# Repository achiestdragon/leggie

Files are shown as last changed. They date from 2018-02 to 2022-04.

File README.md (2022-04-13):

# leggie

a hexapod robot

.    still work in progress not all code completed yet 

.    project suspended , the joystick code works well so is left here for others to use 
      had issues with 3d printed parts snapping , not found a good solution to this 
      so have given up on the project , as well as some other health reasons 

# progress:-

hardware build and 3d printed parts :-

.    see README.txt for hardware and printing progress status and notes

.    dc motor version ( current work in progress )

.    3d printing parts of parts 400 hrs total so far 

.    current progress (assembling)

.    TODO:- lots  , add scad/stl parts for upper body&arms

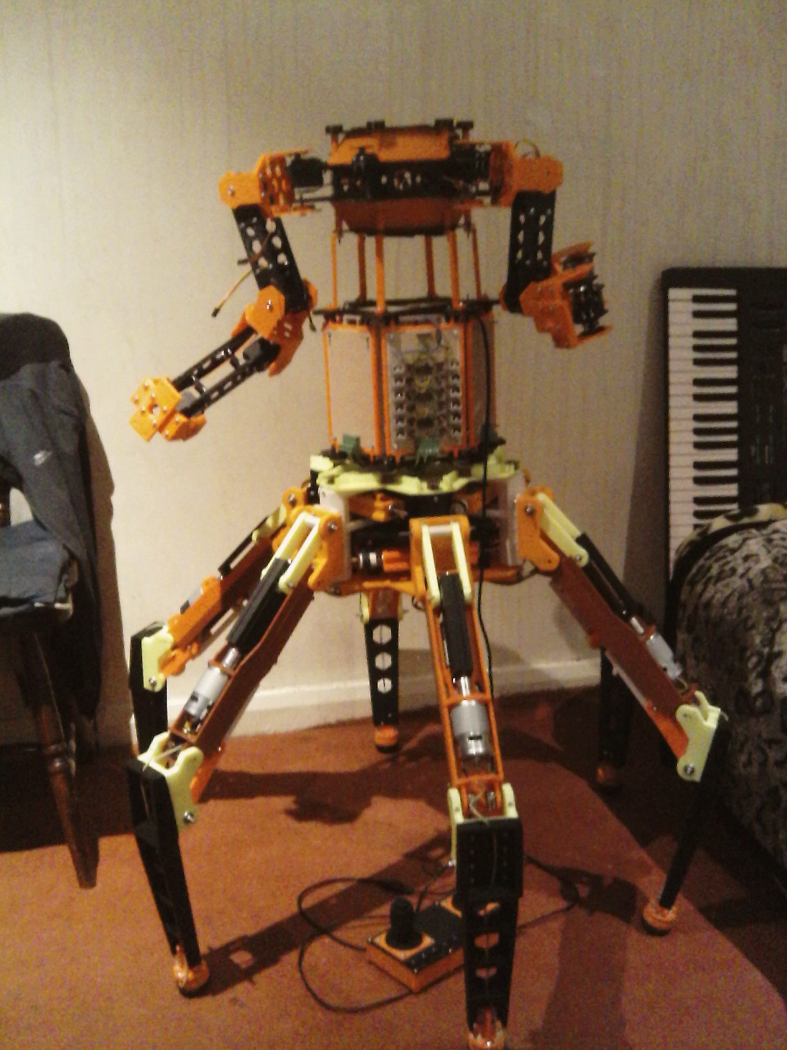
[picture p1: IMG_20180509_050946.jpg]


# code status :-

arduino nano  joystick code :-             USBjoystick1.ino       (c++)= v 1.1b  release

arduino nano  leg drive control code :-    leggie_arduino_pid.ino (c++)= v 1.0a  alpha in progress

..   rewrite pending for dc motor drive rather than pwm servo (will keep this file and add a seperate one

..   for dc motor drive pid   leggie_dc_drive.ini  (c++) = 'pending todo update'

rpi3 serial concurrent test read script :- srlpy.py (python) v 1.0a  a rough but working alpha

raspberry pi3  main control code  :-      main.py (python) v 0.9 in progress not complete

..   basic test code moves legs by joystick and a couple of preprogrammed sequences

see config_guide.txt for software setup and configuration notes

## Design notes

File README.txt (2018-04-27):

leggie  hexapod robot project version 6.0a README.txt

(c)2018 by David Powell  AKA. AchiestDragon

current version :- 6.0a  (alpha prototype)

project status
--------------

 hardware:-
    
    most of the cad redesign is done , although there's still some parts to do
  mainly , electronics covers , battery mounting , turret and head , that can
  wait for the time .
  
    there are a couple of points that may need some of the parts to be reprinted
  mainly the hip/knee joints ( with a diferent infill setting ) as a couple have
  slightly split where the pot mountings have been over tightended , although will
  see how they go as they have not totaly snapped and seem to hold well enough
    the other issues beeing the hip pivot part, this needs a hacksaw to remove on of the
  cross supports so it can actualy be assembled, in genaral all the bearing holes needed
  shaving so the bearings fitted and some of the holes in genaral also needed to be trimmed
  for it to go together.
  
    it takes about a day each to assemble a leg , including the time taken to clean up the
  3d printed parts, and about 2 days to do the main center base assembly , not including 
  print time , you need to ensure its 100 percent before fitting it as servicing it later
  is a real pain , there is an order it needs to be assembled in otherwise you will find 
  your taking it apart again ( should be covered in the assembly guide)
  
    its taken over 324 hrs of 3d printing (and about 6kg of filament used so far)
  the main base and legs of the robot are now all printed and assembled and i 
  am currently about to start work on  the dc motor drives & other electronics.
  
    once the robot can be powered up i can get back on with the software. i also 
  need to include schematics and layouts for the motor drivers and robot wireing
    
    at present im still planning to use a pi3 and adruino nanos for the robot control
  logic , but am still tempted to use a fpga for the motor timings in place of the
  arduino nanos , this is because the responce times are quicker and also the fact that the 
  fpga method can concurrently keep all the motors in sync far easyer than software
    with this in mind i need to keep the electronics more modular so it could be changed 
  if needed, the main issue here though is finding a fpga module with tool chain that
  is firstly not overly expencive and 2nd is going to be arround for some time , 
    as the same is true, of the controlers in genaral making it modular so future
  upgrades and new moddels of controlers may be used in future is also a good step
  
    this version the robot can seperate into 2 distinct parts the lower walking section
  base and legs , and the upper body section , they are joined by some spring and 3d printed 
  clips  , and connectors , that allow them to seperate , this is for transportation , 
  
    the upper electronic frame has mountings for 6 100*160 mm "eurocard" sized pcbs for the motor
  drivers (3 drivers on each ) and another for  interconnections and for the rpi3 to mount on 
  still to cad but the battery mountings , turret and head mountings will also attach to the upper
  assembly , also to cad are the covers for the electronics , but can only do these once the boards
  have been assembled so the component heights and positions can be taken into account , they may also 
  need fan mountings to keep the drivers cool 
  
    batteries , at present i have a couple of options  it needs 24 to 36v for the motors and 5v for the logic
  so i could use 2 14v and 1 7v lipo but dont realy want to have to mix types , and is the reason why i have not 
  done the cad for the battery mountings as yet 
    
    4 of the 7.4v 4000mAh or 2 of the 14.8v lipos batteries in series will give 29.6v  , an a seperate battery for
 the logic so that it does not just shutdown when the main drive power is low 
    
    the higher the voltage the faster rpm of the motors (before torque) , it could run from just 1 11.8v battery
  but it would be slow , current consumption / load is the other issue , and that relates to how long it will run 
  before you need to recharge
  
    the fact that this version is using the motors in a linear motor arrangment means all the legs hold without
  power only needing power to move , over servo versions that need power to the motors to hold there positions
  helps it run longer , the disadvantage is you cant just move the legs by hand without power to them , you have
  to turn the motor drive to get the joint to move , access to be able to do this is possible 

 software:-

    still work in progress (most of current software here relates to the servo 
  version at present and is going to be mostly rewritten )  as support for the 
  servo version is redundant long term it will be removed at some point

 history
-----------
    design history of the current hexapod robot 

    version 1  "tinybug" 
       not that tiny it used cheap satelite dish positioning jacks , suspended
    dew to being too big ( it was almost 10foot across in normal standing pose),
    power and speed with around 1kw full load, 160kg and a walk speed of about
    20 foot an hr  and 1 hr before needing to recharge the 8 x 12v 7ah lead acid gell batteries
    that took about 2 days each time, the joints where very clunky and had mountains 
    of backlash on each leg , and a mini atx controler (2010)
    
    version 2 "scare-e"
       smaller a servo version , it was fpga based and ran out of available gates in the
    fpga , so never was compleated, had 3d ultrasonics , leg movment was by pll locked state machine
    motor control sweet , ran out of gates doing the cpu , (2012)
    
    version 3 "un-named-version" 
       never got passed cad stage , sort of a hybrid concept  of a hexapd with wheels for feet
     so it could use the wheels on flat ground , or switch to walk mode and use them like feet 
     to climb up stairs , nice in concept till you try to do the stair climbing spaceings  then 
     it turns into a monster (2017)
    
    version 4 "un-named-version"
       did cad for this a dc motor version although with smaller motors but decided
      to have another go at a servo version , this one never left the drawing board
      but should of current version is a rework of the ideas i used on this (2017)

    version 5  "leggie " servo version  , scraped , servos not strong enough (2018)
    
    version 6  "leggie6" dc motor version current work in progress(2018)

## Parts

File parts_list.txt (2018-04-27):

parts list

Leggie6 parts list dc motor version
------------------------------------
this list is not complete as yet, work in progress
quant  part 
 18x   rs 775 12 to 36v dc motor 5mm shaft  
 1x    raspberry pi 3 (with 16gb microsd card for software)
 7x    arduino nano 
 36x   10k 6mm potentiometer with D shaft 
 1x    5v 3A switching regulator bec module (for pi/arduino power)
 2x    3 axis joysticks
 10x   push button switches momentary  (12mm dia hole)
 1x    10a single pole single throw on/off toggle switch
 
 3x    short usb a to mini b  cables
 1x    1.5m long usb a to mini b cable for joystick 
 
 1x    7.4v 4000mha lipo  (and suitable charger)
 2x    14.8v lipo's 4000mha (both the same type and charger )
 
 18x   15a 36v h-bridge driver modules (30a peek load) (parts list for this to be added)
 
        bearings (type 625)  5mm shaft 5mm high by 16mm outer dia
        m5 nuts and bolts  25mm thread length
        m5 threaded bar 
        
 18x   5mm to 5mm flexible shaft couplers
 
 36 x  m4 screws for the motor mountings( use screwdriver or alen key heads no room for spanner to fit)

 as needed signal wire in a number of colors
 bag of 50 cable ties (that will fit though 3mm dia holes)
 1x bag of 500 M3 bolts x 18mm long
 1x bag of 500 M3 nuts
 1x bag of 200 M3 locking nuts
 1x bag of 500 M3 washers
 6x 150mm lengths of M3 threaded bar
 10x deans connector pairs and suitable power cable
 8x strip board 100*160mm  for the electronics and motor control boards 
 some solder
 
 lots of other bits not covered yet 
 
 lots of time patience and some thought to get it working

intended for printing on a tevo delta with a 340mm dia print limit 

allow a few weeks for the printing of parts over 324 hrs 

extra parts needed for both versions
------------------------------------

for debug , testing , programming and setup you will need :-
a laptop / or pc to connect to pi3 ether ssh or vnc over wifi or bluetooth

(parts not yet defined ) 
------------------------
leds led drivers and wireing 

some sort of speaker / sounder for the onboard pi3 as it needs some way
of giving status feedback without having a display connected

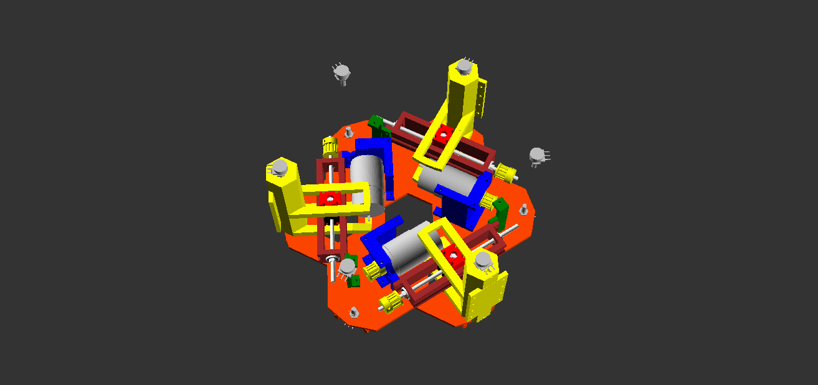
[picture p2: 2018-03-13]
scad_parts_dc_motor_version/base_asembled1.png

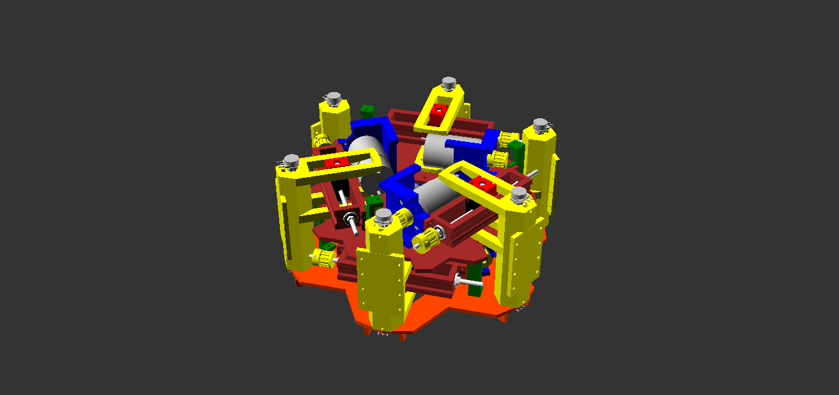
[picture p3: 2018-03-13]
scad_parts_dc_motor_version/base_asembled2.png

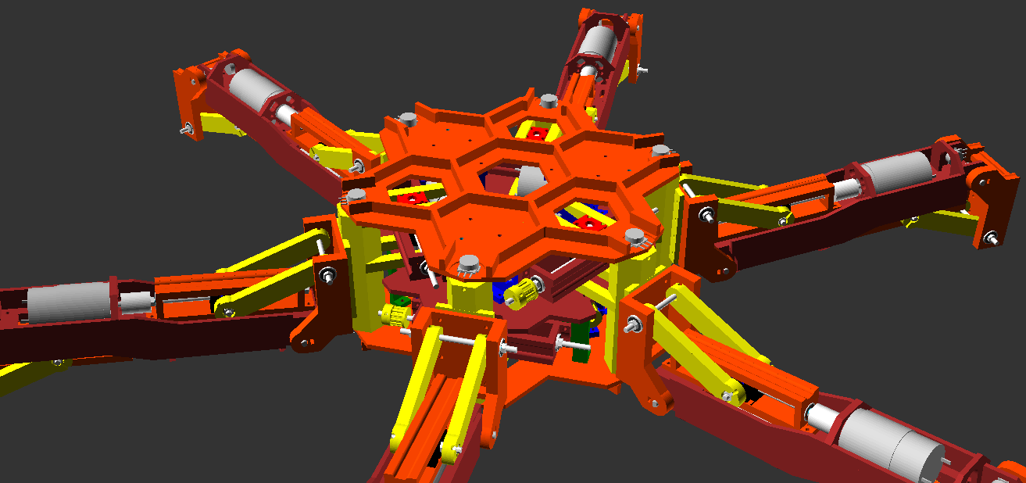
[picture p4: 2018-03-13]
scad_parts_dc_motor_version/base_asembled3.png

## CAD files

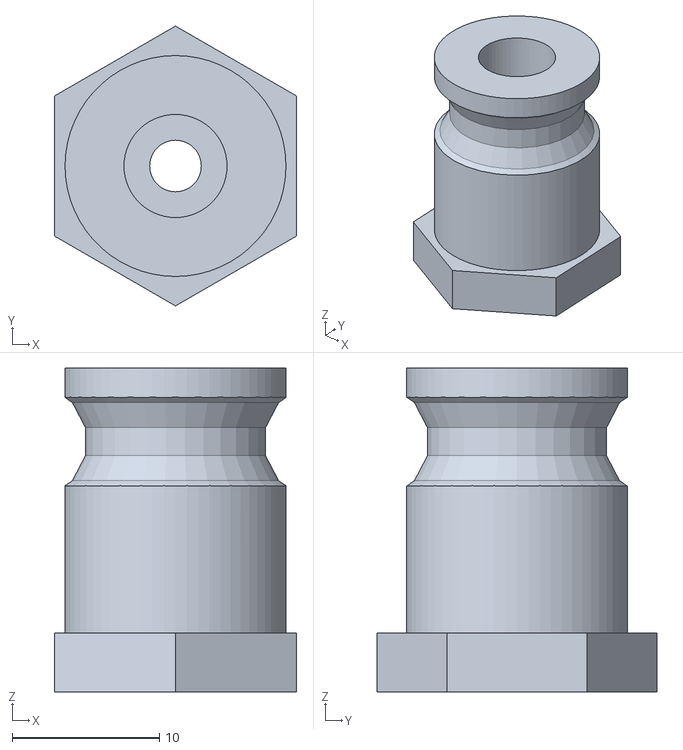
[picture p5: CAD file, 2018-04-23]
stl_parts_dc_motor_version/bodymount.stl
16.5 x 19.0 x 22.0

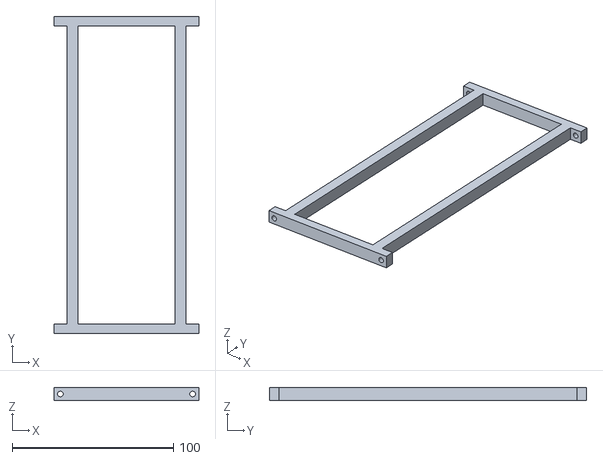
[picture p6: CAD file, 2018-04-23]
stl_parts_dc_motor_version/spacerframe.stl
90.0 x 197.0 x 8.00

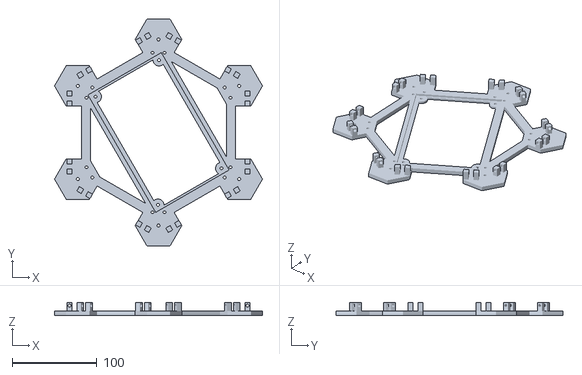
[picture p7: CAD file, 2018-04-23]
stl_parts_dc_motor_version/upperbodyt.stl
245.5 x 267.6 x 15.0

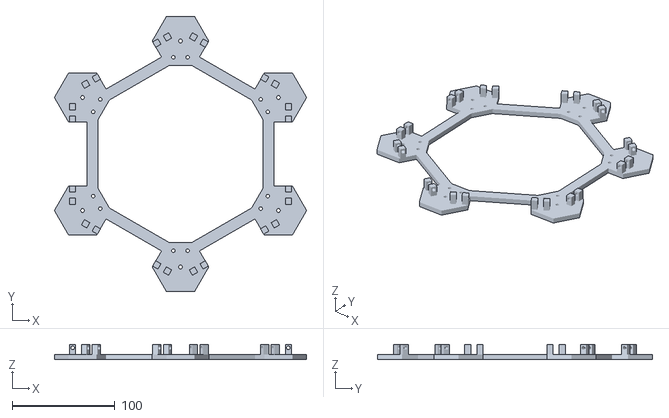
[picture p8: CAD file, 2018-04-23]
stl_parts_dc_motor_version/upperbodyb.stl
245.5 x 267.6 x 15.0

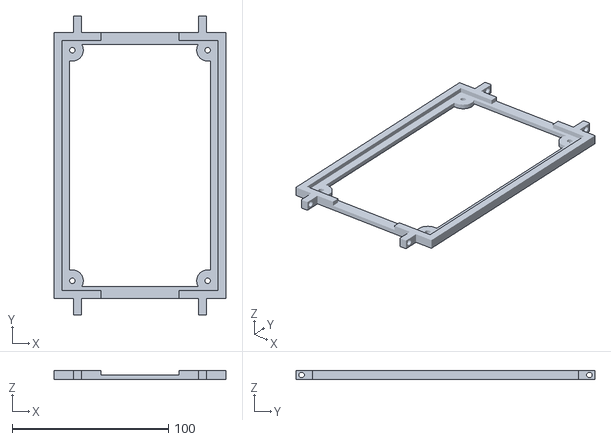
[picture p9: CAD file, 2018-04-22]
stl_parts_dc_motor_version/pcbmountframe.stl
110.0 x 191.0 x 6.00

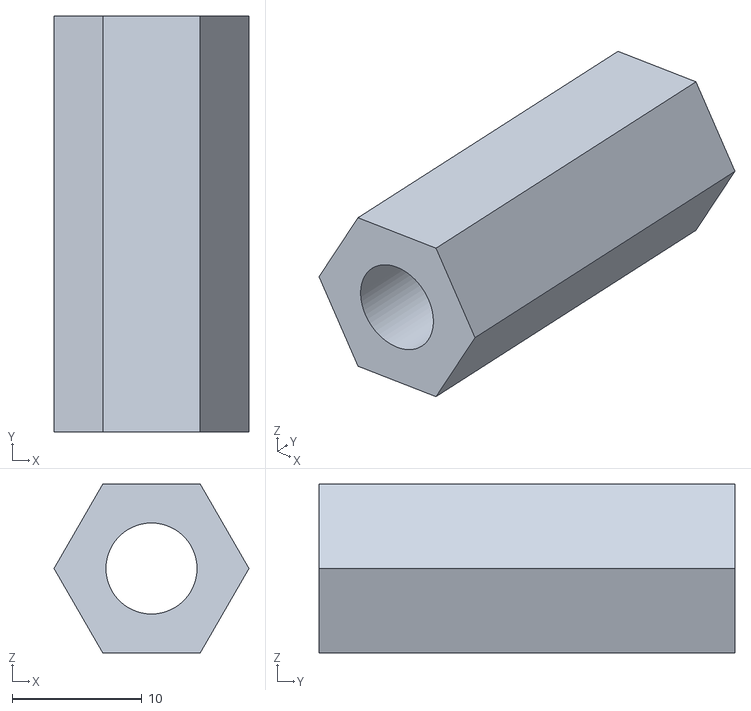
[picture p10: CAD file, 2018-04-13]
stl_parts_dc_motor_version/conrod_spacer.stl
15.0 x 32.0 x 13.0

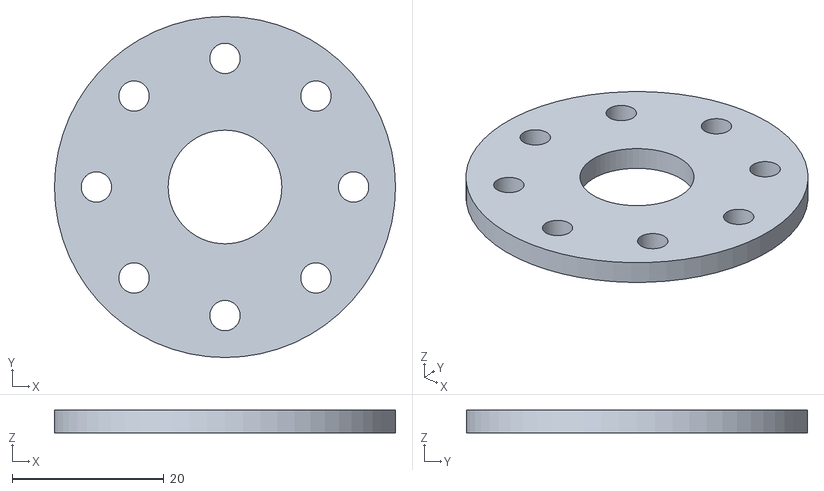
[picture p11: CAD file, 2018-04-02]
stl_parts_dc_motor_version/footsw1.stl
45.0 x 45.0 x 3.00

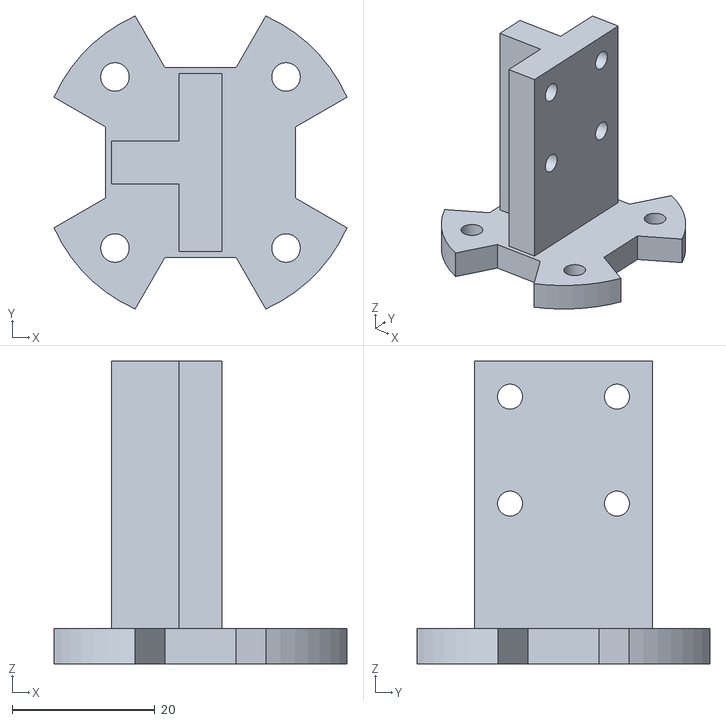
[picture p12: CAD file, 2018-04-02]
stl_parts_dc_motor_version/foot_mnt.stl
41.1 x 41.1 x 42.5

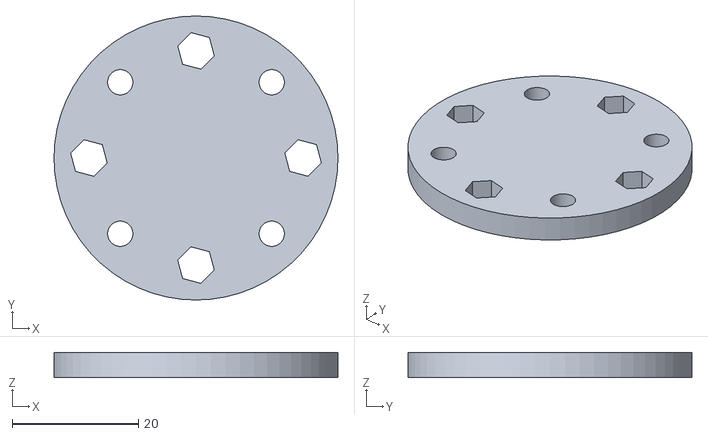
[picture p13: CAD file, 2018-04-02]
stl_parts_dc_motor_version/footsw4.stl
45.0 x 45.0 x 4.00

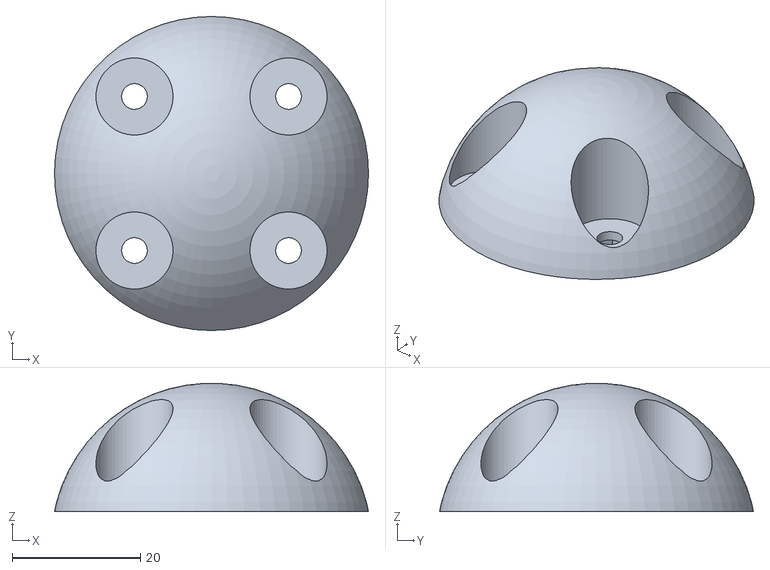
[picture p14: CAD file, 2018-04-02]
stl_parts_dc_motor_version/footpad.stl
48.9 x 48.9 x 20.0

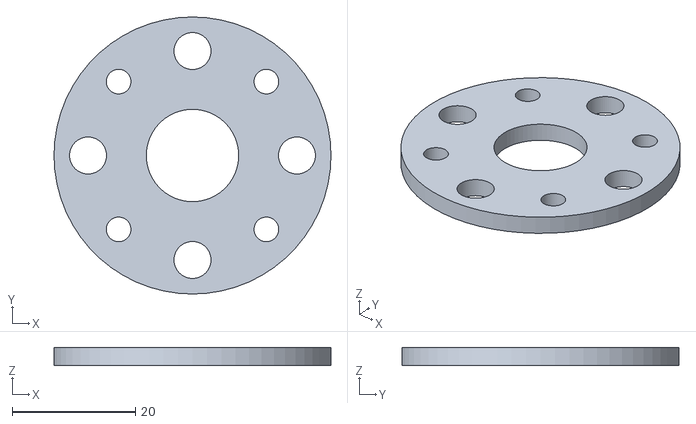
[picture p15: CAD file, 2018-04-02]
stl_parts_dc_motor_version/footsw3.stl
45.0 x 45.0 x 3.00

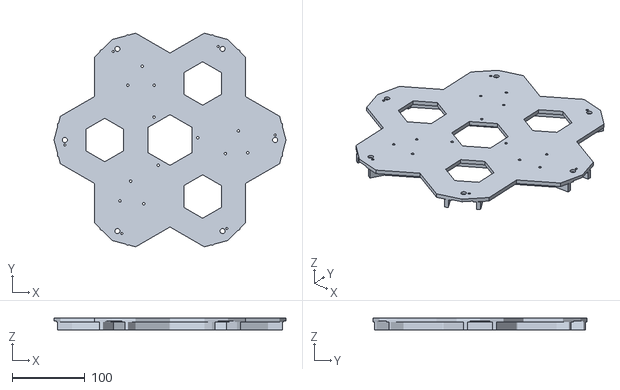
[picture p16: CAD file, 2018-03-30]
stl_parts_dc_motor_version/base_bottom.stl
320.0 x 294.6 x 16.0

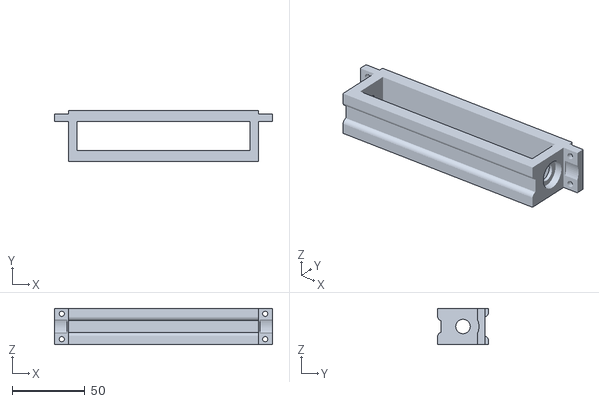
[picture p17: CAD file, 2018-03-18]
stl_parts_dc_motor_version/actuator_shaft_rail.stl
150.0 x 35.0 x 25.0

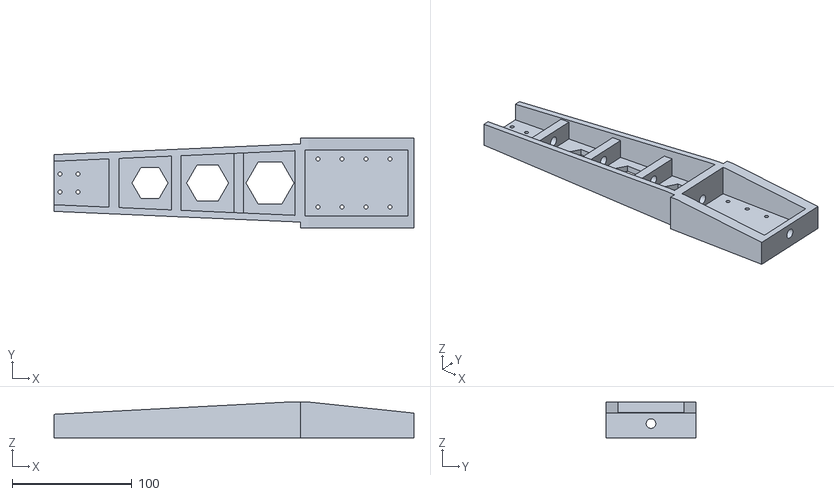
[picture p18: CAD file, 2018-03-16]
stl_parts_dc_motor_version/lower_leg.stl
300.0 x 75.0 x 30.0

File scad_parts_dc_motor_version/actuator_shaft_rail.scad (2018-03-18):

// actuator_shaft_rail.scad
//
//*****************************************************************************
//*             (c) 2017 by David Powell (aka AchiestDragon)                  *
//*****************************************************************************
// Notes :-
// 
//

// ****************************************************************************
// Libraries :-     (local directory libs) 


include <shapes.scad>


//*****************************************************************************
// Code :-


rotate([90,0,0]){    shaft_rail();}

module shaft_rail()
{ 
  color("yellow",1)
  {
    translate([77.5,0,0])
    { 
      difference()
      {
        union()
        {
          translate([-62.5,0,20]){cube([6,25,30],center=true);}
          translate([62.5,0,20]){cube([6,25,30],center=true);}
          translate([0,0,32.5]){cube([131,25,5],center=true);}
          translate([0,0,7.5]){cube([150,25,5],center=true);}
          
          translate([0,9.5,34.5]){cube([131,6,6],center=true);}
          translate([0,11,5.5]){cube([131,3,6],center=true);}
          translate([0,-9.5,34.5]){cube([131,6,6],center=true);}
          translate([0,-11,5.5]){cube([131,3,6],center=true);}
          
          translate([0,7,34.5]){rotate([0,90,0])cylinder(h=131,d=6,center=true,$fn=60);}
          translate([0,9.5,5.5]){rotate([0,90,0])cylinder(h=131,d=6,center=true,$fn=60);}
          translate([0,-7,34.5]){rotate([0,90,0])cylinder(h=131,d=6,center=true,$fn=60);}
          translate([0,-9.5,5.5]){rotate([0,90,0])cylinder(h=131,d=6,center=true,$fn=60);}
        }
        translate ([-3.5,0,20])rotate([0,90,0])
        {
          translate([0,0,-60]){rotate([0,180,0]){cylinder(h=5,d=16,center=true,$fn=60);}}
          translate([0,0,-60]){rotate([0,180,0]){cylinder(h=30,d=10,center=true,$fn=60);}} 
          translate([0,0,67.5]){rotate([0,180,0]){cylinder(h=5,d=16,center=true,$fn=60);}}
          translate([0,0,67.5]){rotate([0,180,0]){cylinder(h=30,d=10,center=true,$fn=60);}} 
          translate([0,0,85]){rotate([0,180,0]){cylinder(h=30,d=22,center=true,$fn=60);}}
          translate([0,0,-78]){rotate([0,180,0]){cylinder(h=30,d=22,center=true,$fn=60);}}
        }
        {Cubic_Array (140,17.5,0,2,2,1,center=true){ rotate([0,0,0]){cylinder(h=30,d=3.5,center=true,$fn=60);}}}
      }
    }
  }
}

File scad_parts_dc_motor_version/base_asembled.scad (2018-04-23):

// base.scad
//
//*****************************************************************************
//*             (c) 2017 by David Powell (aka AchiestDragon)                  *
//*****************************************************************************
// Notes :-
// 

//  included libs are none printable parts for positional /cutouts & assembly
//  guides unless otherwise stated


// ****************************************************************************
// Libraries :-     (local directory libs) 
include <MCAD/units/metric.scad>
include <MCAD/hardware/bearing.scad>
include <MCAD/fasteners/metric_fastners.scad>

include <shapes.scad>
include <parts_lib.scad>
include <leg_joints.scad>
include <leg_joint.scad>

//*****************************************************************************
// Code :-
//translate([0,0,-60])printer_bed();
//base_bottom();
asm();
module asm()

  {
  // hip motors and slides
  upper();  
  lower();
  
  // hip sence pots
  translate([0,0,-70])rotate([0,0,30])Radial_Array(60,6,145){translate([0,0,2.5])rotate([0,0,90])pot();}
  translate([0,0,70])rotate([0,180,0])rotate([0,0,30])Radial_Array(60,6,145){translate([0,0,2.5])rotate([0,0,90])pot();}
  //base plates
  base_bottom();
  base_top();
  base_center();
  
  //legs
  // full assembled legs or.. 
  translate([0,0,-21])rotate([0,0,30])Radial_Array(60,6,346.5){rotate([180,-6,90])fullasm();}
  translate([0,0,8])rotate([0,0,30])Radial_Array(60,6,486.5){rotate([0,-90,-90])leg();}
  // just leg hip joint plates
  //translate([0,0,5])rotate([0,0,30])Radial_Array(60,6,197.5){rotate([180,-0,90])end_joint1();}
  hip_pivot_asm();
  translate([0,0,5])upper_body_mount_asm();
    bodymount1(); 
  }
  
module upper_body_mount_asm()
  {
   upperbody();
   translate([0,0,392])rotate([0,180,0]) upperbodyt();
   //pcbs

    translate([0,0,196])rotate([0,0,30])Radial_Array(60,6,105)rotate([-90,0,0])pcbmountframe(); 
    translate([0,0,196])rotate([0,0,30])Radial_Array(60,6,105)rotate([-90,0,0])eurocard();
    
   // inner frame  
   translate([0,0,196])rotate([0,0,30])Radial_Array(60,6,85)rotate([-90,0,0])spacerframe(); 
   
 }
module spacerframe()
 {
   color("white",1)difference()
     {
       cube ([90,197,8],center=true);
       translate([42,0,0])cube ([10,185,9],center=true);
       translate([-42,0,0])cube ([10,185,9],center=true);
       cube ([60,185,9],center=true);
       
       translate([-41,0,0])rotate([90,0,0])cylinder(h=300,d=3.5,center=true,$fn=60);
       translate([41,0,0])rotate([90,0,0])cylinder(h=300,d=3.5,center=true,$fn=60);
     }  
 }
module pcbmountframe()
 {
   color ("orangered",1)
   {
     difference()
     {
       cube ([110,170,6],center=true);
       translate ([0,0,4])cube ([100,160,8],center=true);
       translate ([0,00,4])cube ([50,200,8],center=true);
       cube ([90,155,8],center=true);
      
     }
    translate([0,0,-1.5]) Cubic_Array(86.5,147.5,0,2,2,1,center=true){ring (14,3.5,3,60);} 
    translate([-40,90,0]) rotate([0,90,0]) difference(){cube([6,11,5],center=true);translate([0,2,0])cylinder(h=20,d=3.5,center=true,$fn=60);}
    translate([40,90,0]) rotate([0,90,0]) difference(){cube([6,11,5],center=true);translate([0,2,0])cylinder(h=20,d=3.5,center=true,$fn=60);}
    translate([-40,-90,0]) rotate([0,90,0]) difference(){cube([6,11,5],center=true);translate([0,-2,0])cylinder(h=20,d=3.5,center=true,$fn=60);}
    translate([40,-90,0]) rotate([0,90,0]) difference(){cube([6,11,5],center=true);translate([0,-2,0])cylinder(h=20,d=3.5,center=true,$fn=60);} 
   }
   
 }
module upperbodyt()
 {
 color("green",1)
   {
     translate([0,0,95])
     difference()
     {
       union()
       
     {
       Radial_Array(60,6,110)rotate([0,0,0])ring (55,4,5,6);
       
       translate([0,0,0])rotate([0,0,30]) ring (210,185,5,6);
        
    
       translate([0,0,97])rotate([0,0,30])Radial_Array(60,6,105)rotate([-90,0,0])
       { 
       translate([-34,90,0]) rotate([0,90,0]) difference(){cube([6,11,6],center=true);   translate([0,-2,0])cylinder(h=20,d=3.5,center=true,$fn=60);}
       translate([34,90,0]) rotate([0,90,0]) difference(){cube([6,11,6],center=true);translate([0,-2,0])cylinder(h=20,d=3.5,center=true,$fn=60);}  
       translate([-46,90,0]) rotate([0,90,0]) difference(){cube([6,11,6],center=true);translate([0,-2,0])cylinder(h=20,d=3.5,center=true,$fn=60);}
       translate([46,90,0]) rotate([0,90,0]) difference(){cube([6,11,6],center=true);  translate([0,-2,0])cylinder(h=20,d=3.5,center=true,$fn=60);} 
       }
       translate ([0,0,0])rotate([0,0,30])cube ([110,170,5],center=true);
    // 
      }
    translate([0,0,192])rotate([0,0,30])Radial_Array(60,6,85)rotate([-90,0,0])translate([-41,0,0])rotate([90,0,0])cylinder(h=800,d=3.5,center=true,$fn=60);
   
       translate([0,0,192])rotate([0,0,30])Radial_Array(60,6,85)rotate([-90,0,0])translate([41,0,0])rotate([90,0,0])cylinder(h=800,d=3.5,center=true,$fn=60); 
  
   
       
       translate ([0,0,4])rotate([0,0,30])cube ([100,160,8],center=true);
       
       translate ([0,00,0])rotate([0,0,30])cube ([90,155,8],center=true);
      
     
      
    }
   translate([0,0,93.75]) rotate([0,0,30])Cubic_Array(86.5,147.5,0,2,2,1,center=true){ring (14,3.5,2.5,60);}
   } 
 }  
 
module bodymount1()
{
  translate([0,0,74])Radial_Array(60,6,110)
  {
    bodymount();
  }
}
    
module bodymount()
{ color("blue",1)
  { 
  difference()
  {
   union()
  {  
  rotate([0,0,30])ring (19,5,4,6);
  ring (15,3.5,4,60);  
  translate([0,0,10])ring (15,7,20,60);
  }
  translate([0,0,15])torus(10,4,360);
}
}
} 
module upperbody()
 {
 color("blue",1)
   {
     translate([0,0,95])
     difference()
     {
       union()
       
     {
       Radial_Array(60,6,110)rotate([0,0,0])ring (55,4,5,6);
       
     translate([0,0,0])rotate([0,0,30]) ring (210,185,5,6);
    
    translate([0,0,97])rotate([0,0,30])Radial_Array(60,6,105)rotate([-90,0,0]){ 
    translate([-34,90,0]) rotate([0,90,0]) difference(){cube([6,11,6],center=true);translate([0,-2,0])cylinder(h=20,d=3.5,center=true,$fn=60);}
    translate([34,90,0]) rotate([0,90,0]) difference(){cube([6,11,6],center=true);translate([0,-2,0])cylinder(h=20,d=3.5,center=true,$fn=60);}  
      translate([-46,90,0]) rotate([0,90,0]) difference(){cube([6,11,6],center=true);translate([0,-2,0])cylinder(h=20,d=3.5,center=true,$fn=60);}
    translate([46,90,0]) rotate([0,90,0]) difference(){cube([6,11,6],center=true);translate([0,-2,0])cylinder(h=20,d=3.5,center=true,$fn=60);} 
     }
   }
   translate([0,0,192])rotate([0,0,30])Radial_Array(60,6,85)rotate([-90,0,0])
  translate([-41,0,0])rotate([90,0,0])cylinder(h=800,d=3.5,center=true,$fn=60);
   
       translate([0,0,192])rotate([0,0,30])Radial_Array(60,6,85)rotate([-90,0,0])translate([41,0,0])rotate([90,0,0])cylinder(h=800,d=3.5,center=true,$fn=60); 
 } 
   } 
 } 
module base_bottom()
  {
    difference()
    {
    translate([0,0,-70])base_half();
    rotate([0,0,0])
      {
        m_holes_l() ; 
        rotate([180,0,30])Radial_Array(-120,3,50){translate([72.5,0,30])rotate([0,-90,0])rail_end_mount_h();}
      }
    }
  }
  
module base_top() 
  {
    difference()
    {
    color("yellow",1)translate([0,0,70])rotate([0,180,0])base_half();
    rotate([0,0,60])
      {
        m_holes_l(); 
        rotate([180,0,30])Radial_Array(-120,3,50){translate([72.5,0,-30])rotate([0,-90,0])rail_end_mount_h();}
      }
      Radial_Array(-60,6,110){cylinder (h=200,d=4,center=true,$fn=60);}
    }
  }
module hip_pivot_asm()
  {
    rotate([0,180,-30])Radial_Array(120,3,145){rotate([0,0,-90])hip_pivot();}
    //rotate([0,180,-30])Radial_Array(120,3,145){rotate([0,0,-45])hip_pivot();}
    //rotate([0,180,-30])Radial_Array(120,3,145){rotate([0,0,-135])hip_pivot();}
    
    rotate([0,180,-30])Radial_Array(120,3,95){rotate([0,0,-90])hip_slide();}
    translate([0,0,-70])rotate([0,0,-30])Radial_Array(120,3,95){rotate([0,0,-90])hip_slide();}
    
    rotate([0,0,30])Radial_Array(120,3,145){rotate([0,0,-90])hip_pivot();}
    //rotate([0,0,30])Radial_Array(120,3,145){rotate([0,0,-45])hip_pivot();}
    //rotate([0,0,30])Radial_Array(120,3,145){rotate([0,0,-135])hip_pivot();}
    
    translate([0,0,70])rotate([0,180,30])Radial_Array(120,3,95){rotate([0,0,-90])hip_slide();}
    translate([0,0,-70])rotate([0,0,-30])Radial_Array(120,3,95){rotate([0,0,-90])hip_slide();}
  }
  
module hip_slide()
  {
    rotate([0,0,0])
    color("red",1)translate([0,0,12])
    difference()
    {
      cube ([25,25,15],center=true);
      translate([0,20,-5])cube ([28,22,17],center=true);
      translate([0,-20,-5])cube ([28,22,17],center=true);
      translate([0,0,1])cylinder (h=3,d1=9,d2=16,center=true,$fn=60);
      translate([0,0,6])cylinder (h=8,d=16,center=true,$fn=60);
      translate([0,0,0])cylinder (h=40,d=9,center=true,$fn=60);
      translate([8,8,-5])cylinder (h=20,d=4,center=true,$fn=60);
      translate([8,-8,-5])cylinder (h=20,d=4,center=true,$fn=60);
      translate([-8,8,-5])cylinder (h=20,d=4,center=true,$fn=60);
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

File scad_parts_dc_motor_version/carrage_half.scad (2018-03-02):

// carrage_half.scad
//
// this is 1 half of the linear actuator carrage (nut holder) 
// 2 off needed for each actuator 
//
//*****************************************************************************
//*             (c) 2017 by David Powell (aka AchiestDragon)                  *
//*****************************************************************************
// Notes :-
// 
// printing
//    print in pla with no supports and 100% infill (as its a small part)  
// 
// ****************************************************************************
// Libraries :-     (local directory libs) 

include <shapes.scad>

//*****************************************************************************
// Code :-


rotate([-90,0,0]){carrage_half();}

module carrage_half()
{
  color("white",1) 
  {
    difference()
    {
    translate([74.,6,20]){cube([30,12,19],center=true);}
    rotate([0,90,0])
      {
        translate([-20,0,74])
        {
          rotate([0,0,0])
          {
            cylinder(h=150,d=6,center=true,$fn=60);
            translate([0,0,0]){rotate([0,0,0]){cylinder(h=18,d=10.5,center=true,$fn=6);}}
            translate([0,0,9]){rotate([0,0,0]){cylinder(h=2,d=11,center=true,$fn=60);}}
            translate([0,0,-9]){rotate([0,180,0]){rotate([0,0,0]){cylinder(h=2,d=11,center=true,$fn=60);}}}
          }
          rotate([90,0,0])Cubic_Array (16.5,10,0,2,2,1,center=true){ {cylinder(h=40,d=4,center=true,$fn=60) ;}}
          rotate([90,0,0])cylinder(h=40,d=6,center=true,$fn=60) ;
          rotate([90,0,0])cylinder(h=15,d=10.5,center=true,$fn=6) ;
          rotate([90,0,0])
          {
            Cubic_Array (13,24,0,2,2,1,center=true){ {cylinder(h=40,d=3.5,center=true,$fn=60) ;}}
            translate([0,0,-25])
              {
              translate([6.5,12,0]) {rotate([0,0,30])cylinder(h=37.5,d=6.7,center=true,$fn=6) ;}
              translate([-6.5,-12,0]) {rotate([0,0,30])cylinder(h=37.5,d=6.7,center=true,$fn=6) ;}
              translate([-6.5,12,0]) {rotate([0,0,30])cylinder(h=37.5,d=7,center=true,$fn=60) ;}
              translate([6.5,-12,0]) {rotate([0,0,30])cylinder(h=37.5,d=7,center=true,$fn=60) ;}
            }
          }  
        } 
      }
    }
  }
}

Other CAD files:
stl_parts_dc_motor_version/leg_joint.stl
stl_parts_dc_motor_version/base_top.stl
stl_parts_dc_motor_version/hip_slide.stl
stl_parts_dc_motor_version/motor_mount.stl
scad_parts_dc_motor_version/conrod.scad
scad_parts_dc_motor_version/conrod_spacer.scad
scad_parts_dc_motor_version/foot.scad
scad_parts_dc_motor_version/hip_pivot.scad
scad_parts_dc_motor_version/hip_slide.scad
scad_parts_dc_motor_version/leg_half.scad
scad_parts_dc_motor_version/leg_joint.scad
scad_parts_dc_motor_version/leg_joints.scad
scad_parts_dc_motor_version/parts_lib.scad
scad_parts_dc_motor_version/rc.scad
scad_parts_dc_motor_version/shapes.scad
stl_parts_dc_motor_version/12_tooth_T5.stl
stl_parts_dc_motor_version/base_center.stl
stl_parts_dc_motor_version/carrage_half.stl
stl_parts_dc_motor_version/conrod.stl
stl_parts_dc_motor_version/hip_pivot.stl
stl_parts_dc_motor_version/leg_half.stl
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

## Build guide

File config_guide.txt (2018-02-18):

leggie robot raspberry pi 3 configuration

1/. setup the rpi to a monitor with keyboard and mouse attached

2/. configure an sd card with noobs and install rasbian 

3/. configure vnc so you can remotely access the pi over wifi
    for this you will need ether a pc , laptop, or other rpi
    and a local wifi network , that should have internet access
    be sure to setup a password other than the pi default one

4/. install the arduino ide on the rpi , this will let you
    program the arduino nanos from the on board rpi using vnc
    remotely so you don't have to connect programming cables
    each time 

5/. create a directory(folder) in /home/pi/Documents  called
    git ,  and open a terminal

> cd Doc*
> cd git
> git clone https://github.com/achiestdragon/leggie.git

this should copy all the needed leggie files to a folder
called leggie in the git folder

6/. now is as good a time as any to program the joystick
    arduino ,  connect the ardruno nano for the joystick
    to the pi by usb , start the ardruino ide set the 
    board and programmer type  load the file USBjoystick1
    and upload it to the nano
    when done go to the serial monitor in the arduino ide
    and you should see the values change with the moment
    of the joysticks and the state of the buttons

6/. power down the rpi , remove keyboard, mouse hdmi and
    joystick
    power up and connect to it using vnc ,you will need
    to set the display resolution on the pi to be at least
    1024*768 as the default 640*480 is too small for the
    arduino window

7/. you  can mount the rpi on the robot and connect up the 
    3 servo control arduinos  , you should now see them as 
    dev/ttyUSB0 1 and 2 in the ardruino ide
    in the ide set the board type as arduino nano and the
    programmer type as arduino as ISP
    
8/. load the file leggie_ardruino_pid in the ide and compile
    select port dev/ttyUSB0 and upload
    wait for it to complete  then select port  dev/ttyUSB1
    upload and wait , and the same for dev/ttyUSB2
    you now should have all 3 arduinos programmed 
    you can check by selecting them by there serial port
    and opening the serial monitor in the arduino ide
    where you should see status messages by pressing the foot
    switches on the legs connected to it 
    
9/. if you are wanting to use the joystick wired to the robot
    then the joystick to the rpi via the remaining usb port
    ( this should make it /dev/ttyUSB3) but it may not be in 
    that order , not that it matters the code sorts it 
    
10/. with robot servo power off but the pi3 and arduino nano's 
    powered , though vnc to the pi cd to 
    ~/Documents/git/leggie/rpi3_code in a console and type
    > python srlpy.py  
    this should run the serial test program  you should get an 
    output from all leg controllers , by pressing the foot switch
    of each leg in any order and if connected a stream of data
    from the joystick that changes when you move the sticks
    or press buttons 
    if so all is good so far

11/. while still connected in the console 
     ctrl+z to exit srlpy.py and type
     > python main.py
     the robot main code should start 
     
     at present this code is not complete but should correctly 
     detect the serial ports and connected devices , and provide
     status messages

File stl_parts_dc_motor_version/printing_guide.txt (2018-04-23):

stl files  individual 3d printable parts  , by david powell AKA (AchiestDragon) license gpl

part                      quant  material  infill      notes                  
------                    -----  --------  ------     ------             
actuator_shaft_rail.stl    18x     pla       20%                     
carrage_half.stl           36x     pla      100%  (supports needed)
conrod.stl                 24x     pla       20%                       
leg_half.stl               12x     pla       20%                        
leg_joint.stl              12x     pla       20%                         
base_top.stl                1x     pla       20%                        
base_center.stl             1x     pla       20%                       
base bottom.stl             1x     pla       20%                        
hip_pivot.stl               6x     pla       20%                        
hip_slide.stl              12x     pla       20%                             
lower_leg.stl               6x     pla       20%                         
motor_mount.stl             6x     pla       20%                          
rail_end_mount.stl          6x     pla       20%                         
footmnt.stl                 6x     pla       20%                         
footsw1.stl                12x     pla       20%
footsw3.stl                 6x     pla       20%
footsw4.stl                 6x     pla       20%
footpad.stl                 6x     flex      20%
conrod_spacer.stl          12x     pla       20%
upperbodyb.stl              1x     pla       20%
upperbodyt.stl              1x     pla       20%
spacerframe.stl             6x     pla       20%
bodymount.stl               6x     pla       20%
pcbmountframe.stl           6x     pla       20%

also required (from other sources)  

12_tooth_T5.stl  (thingverse part #10848 " Printable 12 tooth T5 pulley by AlephObjects" license gpl)
                           12x     pla       100%                         

around 6 x 1kg rolls of filament  approx total 3d printing time      324hrs      

TODO;-   optional upper sections ( head and turrets )cad for these
         battery mountings

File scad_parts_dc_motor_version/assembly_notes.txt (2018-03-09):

assembly.txt

actuator shaft 

see figure 1/. ( actuator_shaft_assembly.png)

place 2  m5 nuts close to the center of the 150mm m5 threaded bar(threads not shown) ,
then 2x 6mm inner dia rubber 'o' rings (shown black on the image) 
with 2 washers

insert 8 short lengths (5 to 9mm long) of 4mm dia ptfe tube (shown as blue on the image)
into the slots on the side  of the carrage halves shown in red

insert  2x m5 (m5*25mm) pivot bearing bolts and fasten in place tight with a nut(nut not shown)

adjust the spacing of the nuts on the theaded bar so they sit snuggly into the carrage halves 
while having a small amount of pressure against the rubber 'o'rings this will remove backlash
but not too much as the threaded bar will be too tight for the motor to turn quickly ,and will
just cause friction and lack of effective power

bolt the 2 haves together using m3 screws (m3*20) and m3 bolts in the outer 4 holes (nuts and bolts not shown)

beraings  on shaft (shown) are added after the above assembly is inserted into the 
actuator_shaft_rail part 

place the shaft and carrage assembly into the actuator shaft rail and it should slide relativily freely
up and down inside the rail , ensure it does not bind and can travel to within 2mm of the ends, (and gives 84mm travel)

fit a bearing at each end and a m5 nut , at one end the shaft the nut holding the bearing should be 
almost flush with the shaft end at the other there should be about 10mm or more of shaft sticking out for the
motor coupling
and also fit a bearing to each m5 pivot bolts and fasten each in place with another m5 nut

Note :- removing the threaded bar from the carrage will require the carrage to be dismantled in order to set the
anti-backlash tension 

leg assembly :-

fig2 upper_leg_assembled.png

fasten the 2 leg halves together using 4 m3 nuts and bolts  insert the assembled actuator rails and fasten them in place
also with m3 nuts and bolts  taking note that  at the outer ends the bolts go up though the leg halves then though the actuators , and at the coupling ends the bolts go down though the actuator rail into the leg halves , this is so the excess threads don't bind with other parts , you will also have to attach a pair of conrods to the ends of the pivot
bearings before placing the actuator rail assembly into the leg half, make sure you also insert some short lenths (3 to 5mm long )of 4mm dia ptfe tube into the 5 slots on the conrods  

attach the shaft coupler to the actuator (you need to push it though the motor output shaft hole),
then mount the motor m4* (lengths for these need to be measured so as there not too long )

and mount the pots and hip/knee pivot plate  (you may have to widen the pot mounting holes) the wireing pins for the pot should face out as per fig2 so you can solder wires to them after there mounted (and also so you can get to them to meter out values when servicing )
you will have to push the pot mounting nut and washer though the gap between the leg base and the hip/knee pivot plate and tighten them with a spanner (this hip/knee pivot plates canot be removed without removing at least one of the pots)
insert a m3 nut into each slot in the pivot plate and a m3 screw , tighten the screws so it grips the d shafts on the pots

insert a m5 bolt though the end of each conrod , and bearings into the pivot plates , then pass the bolt though the bearing and hold it in place with a m5 locking nut

there are 2 holes each side of the motor mountings and 2 slotted holes for wireing to pass though

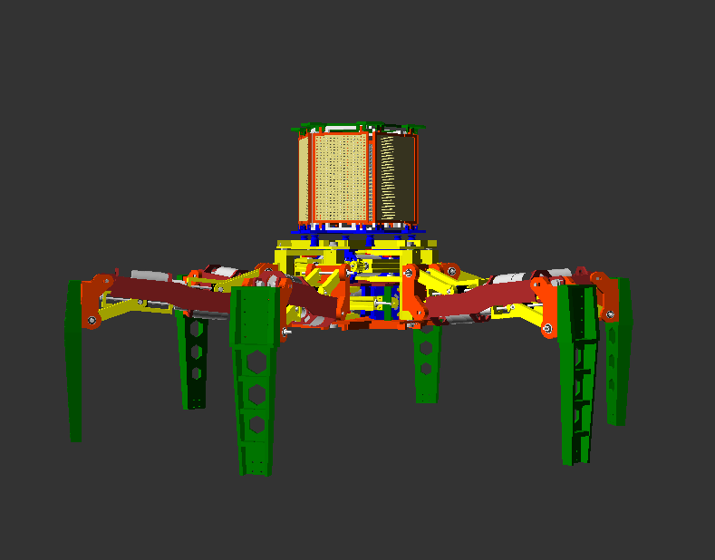
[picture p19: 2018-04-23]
scad_parts_dc_motor_version/assembled.png

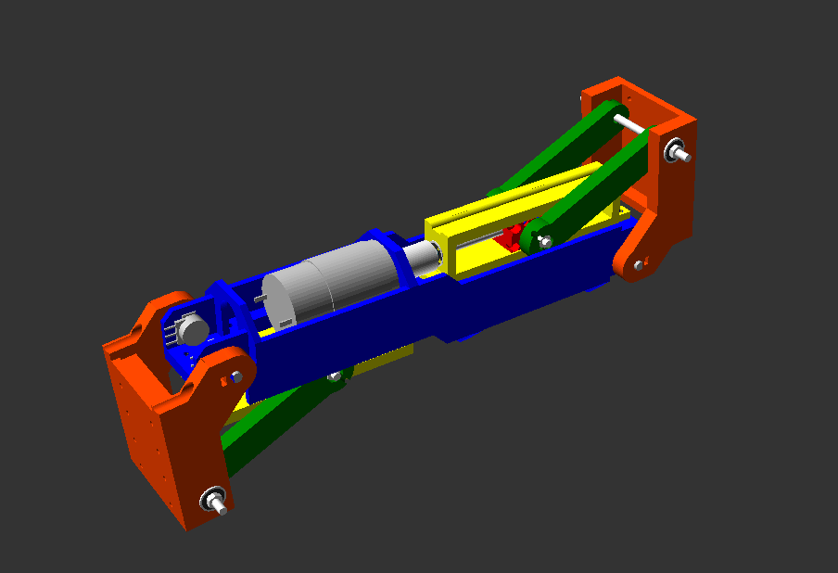
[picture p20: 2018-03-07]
scad_parts_dc_motor_version/upper_leg_assembled.png

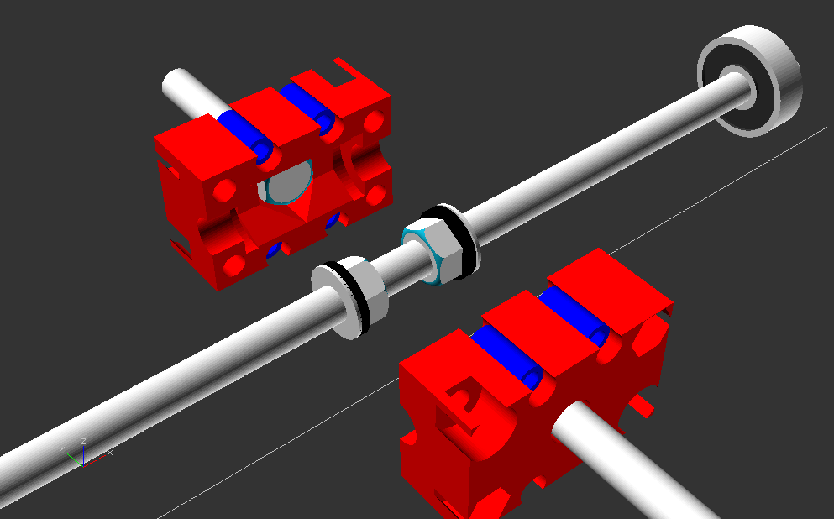
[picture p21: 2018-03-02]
scad_parts_dc_motor_version/actuator_shaft_assembly.png

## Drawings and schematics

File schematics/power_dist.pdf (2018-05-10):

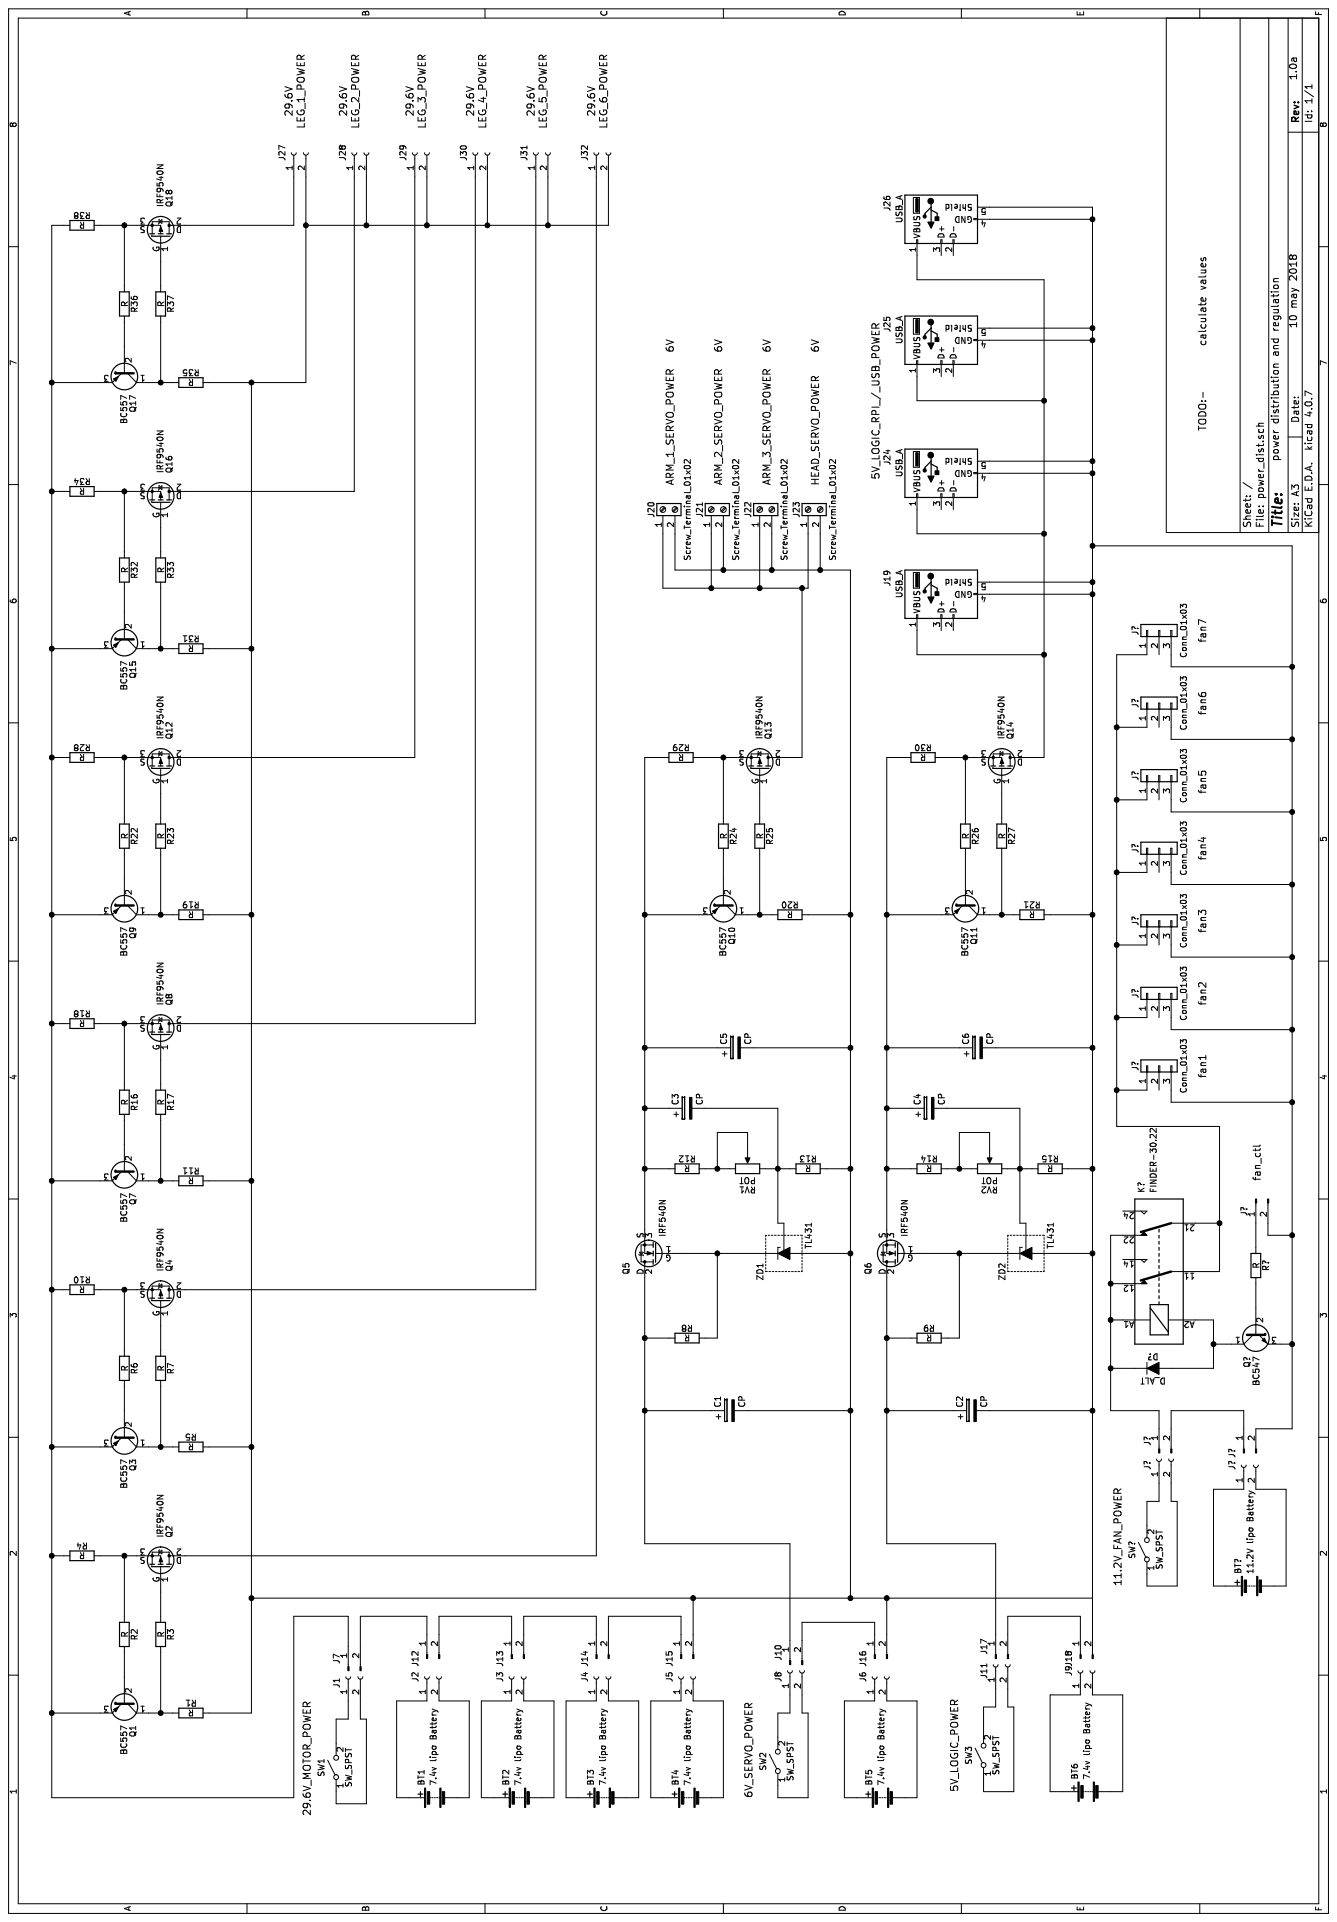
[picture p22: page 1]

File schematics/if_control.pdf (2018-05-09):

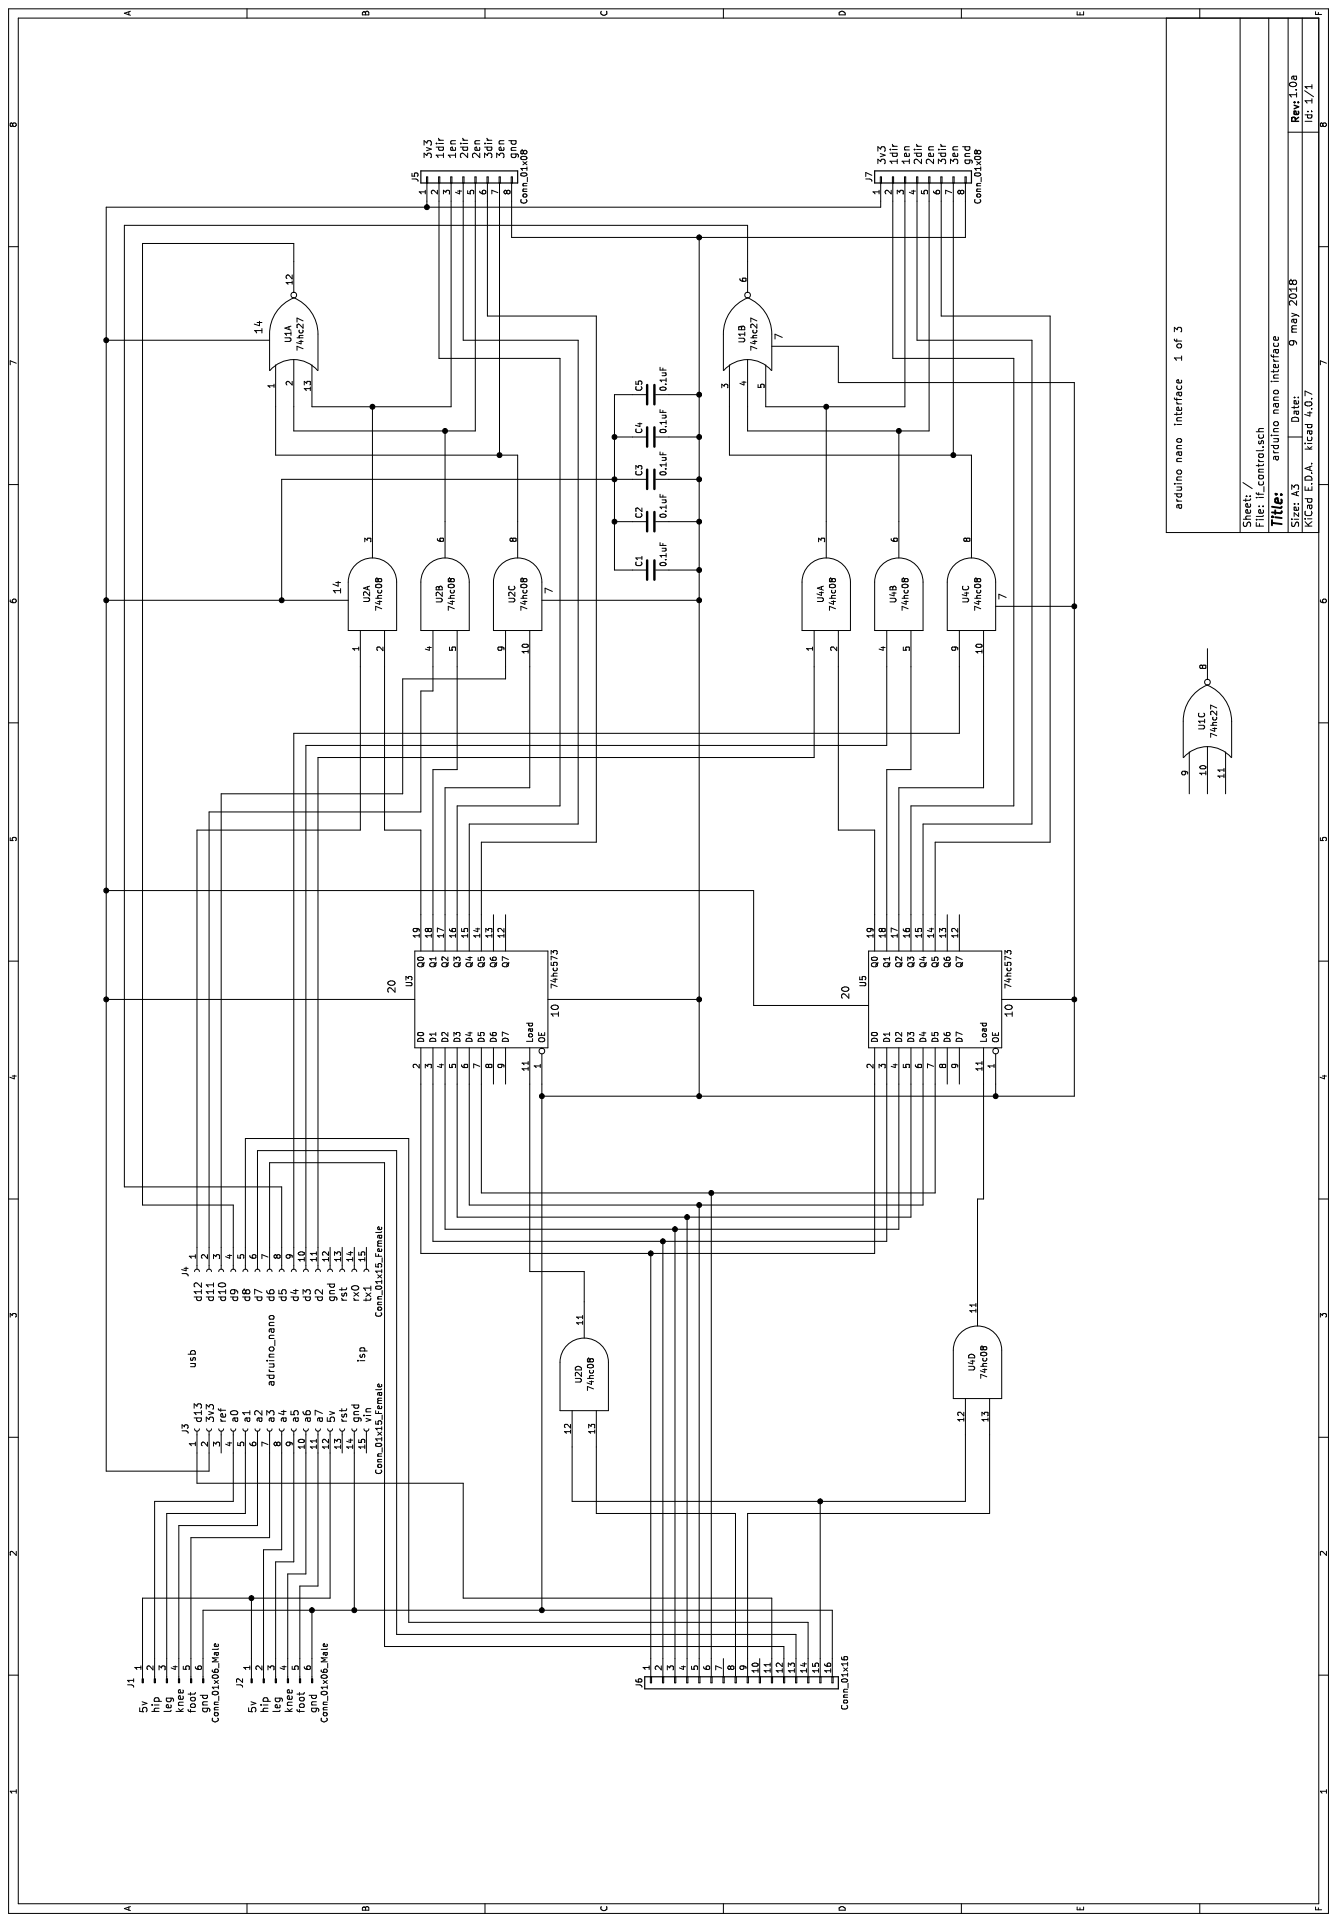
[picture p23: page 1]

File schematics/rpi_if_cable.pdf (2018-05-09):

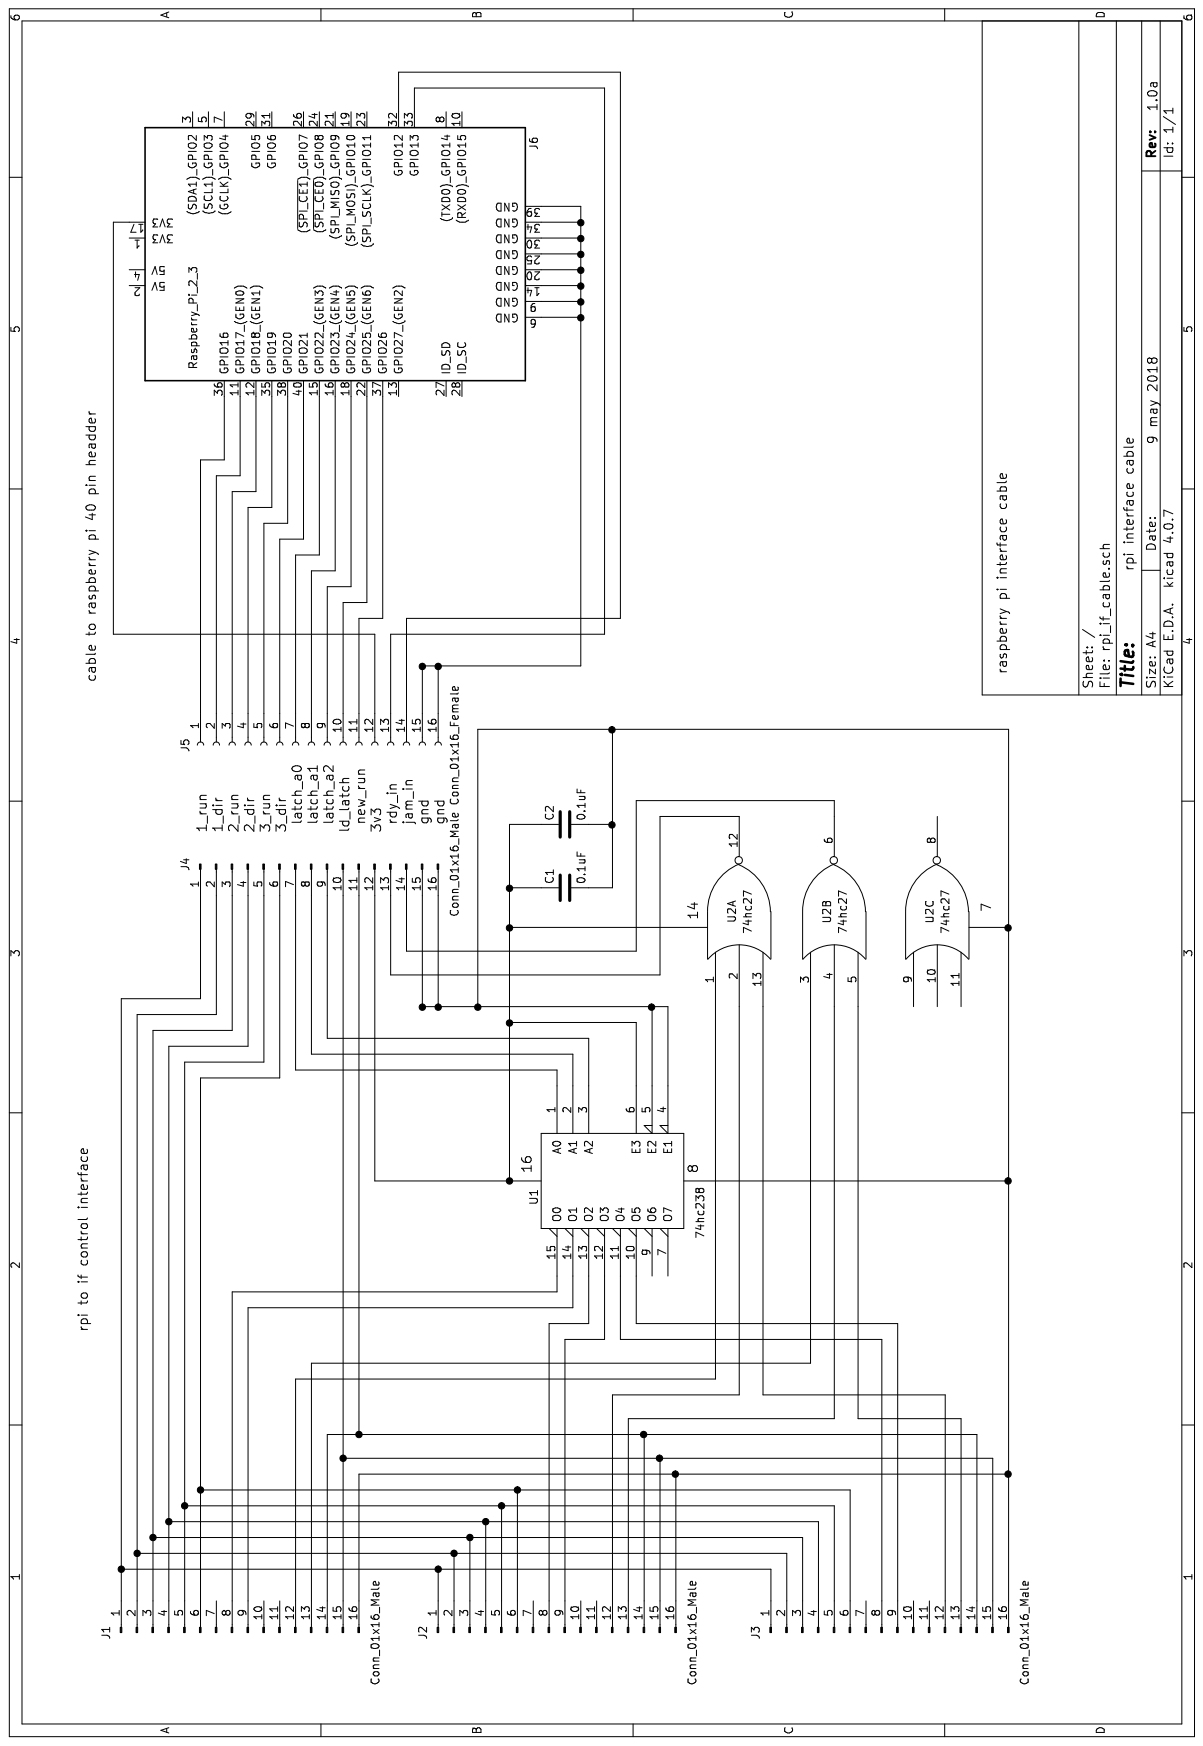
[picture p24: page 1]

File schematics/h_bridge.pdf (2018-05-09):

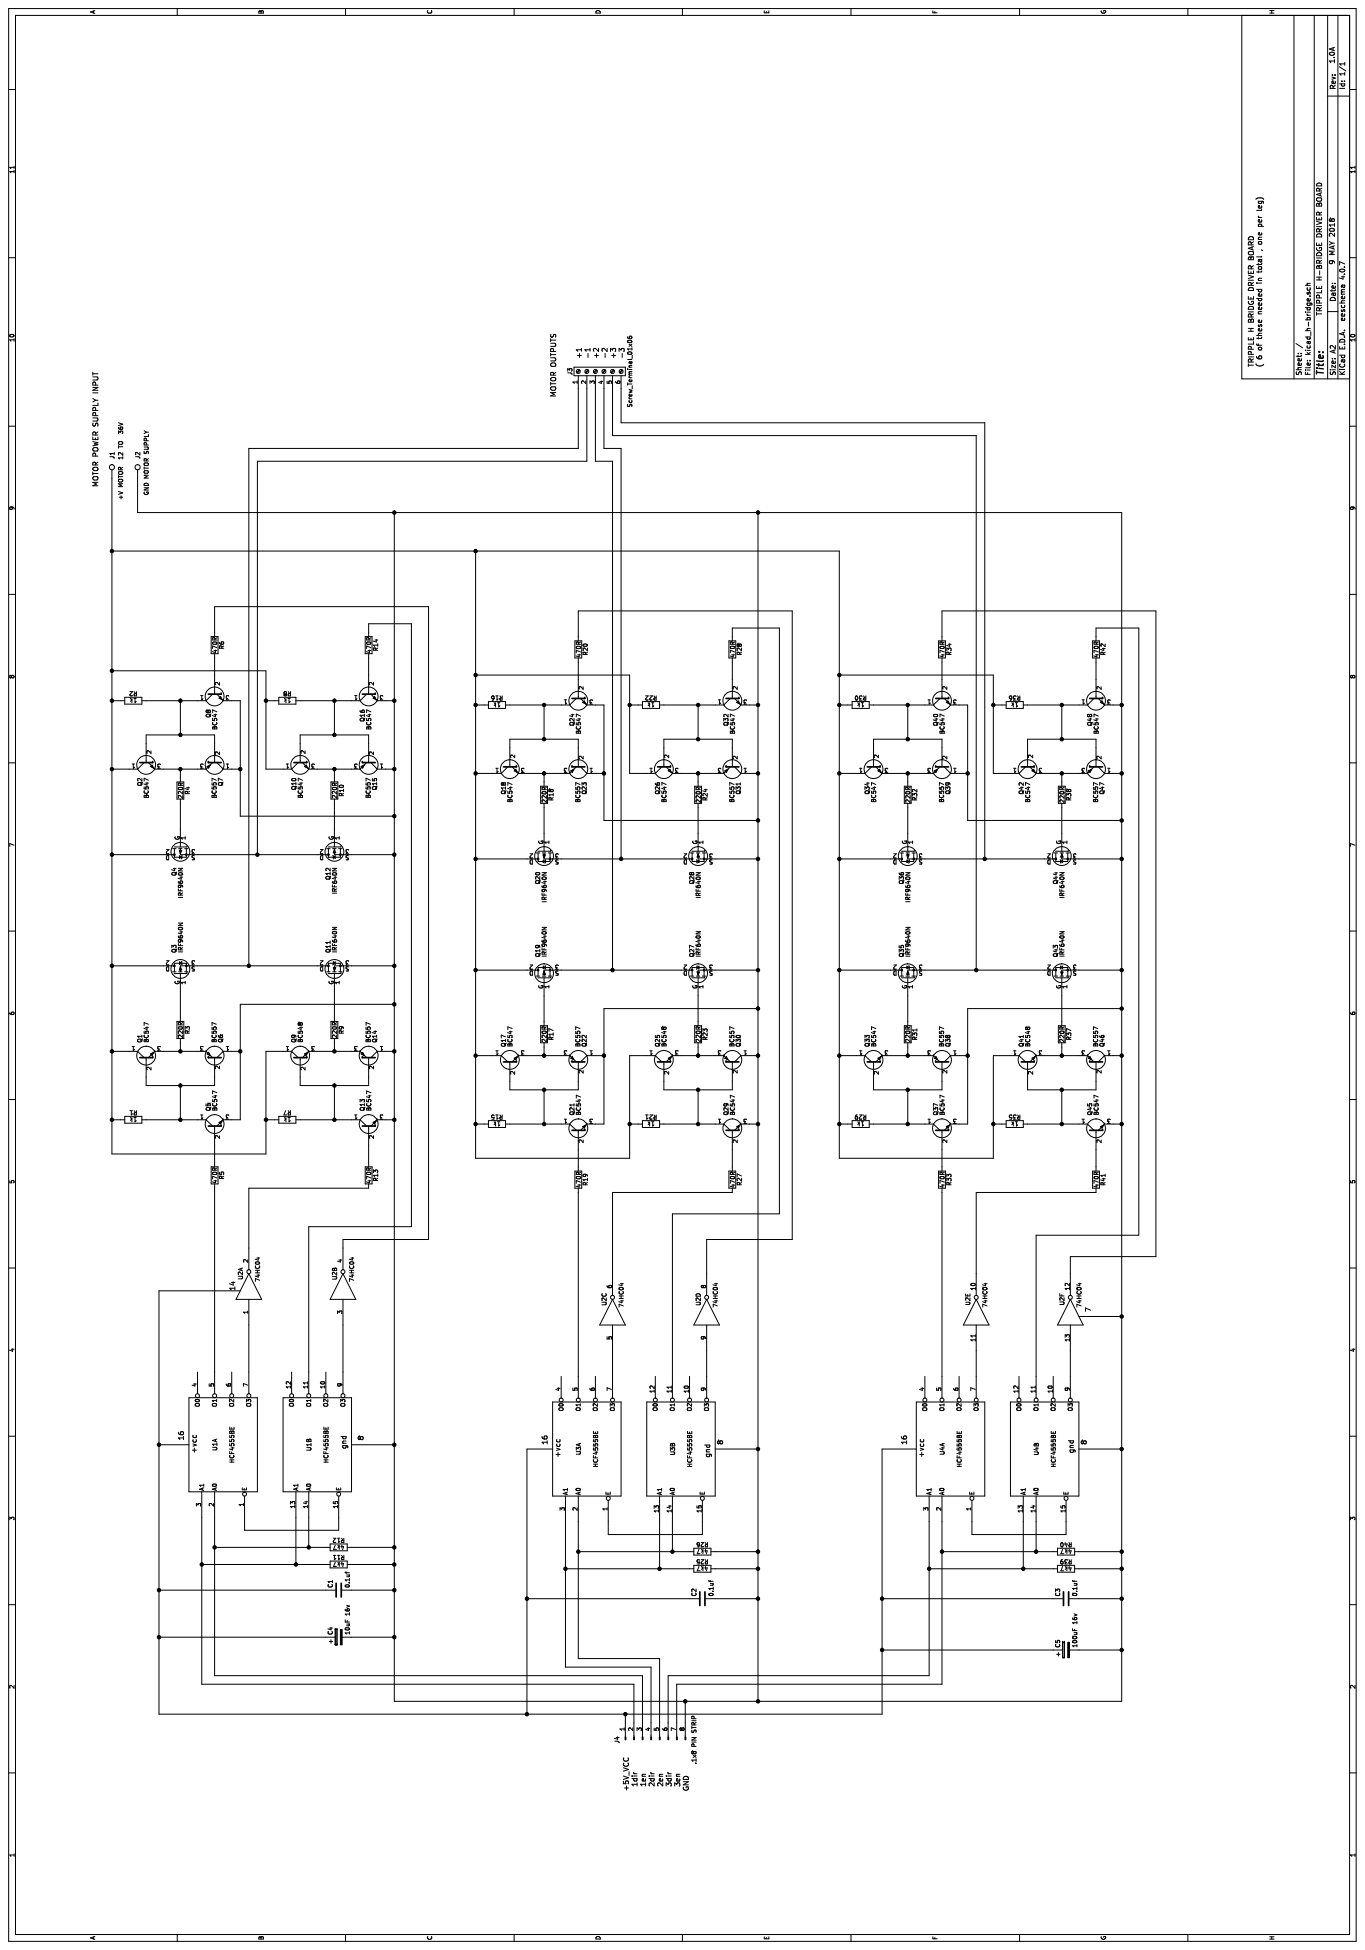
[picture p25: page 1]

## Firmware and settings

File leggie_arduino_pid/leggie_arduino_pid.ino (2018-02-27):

// **********************************************************************
// * leggie arduino servo pid control   version 1.0a alpha   6 feb 2018 *
// **********************************************************************
// *      (c) 2018 & written by david powell (aka AchiestDragon)        *
// **********************************************************************
//   licence :-    GPL V3
/*

discription:-

pid servo contoler for leggie robot
there are 3 ardunio nano's used in total each controling 2 legs
and all running the same code each set as a different address
by the adr0 and adr1 pins  jumper to gnd 
(pullups set on inputs so a jumper on pin = pull down=0)

adr0  adr1    legs
0     0       1 and 2       ( ardunio 1 )
1     0       3 and 4       ( ardunio 2 )
0     1       5 and 6       ( ardunio 3 )
1     1       calibrate / test mode ,

in calibrate /test mode it returns a extended packet with actual 
adc read values , scaled values and foot status 

the 3 arduino nanos are wired by short usb leads to the onboard 
raspberry pi3 where they also get there power
the pi3 gets its power from one of the 5v 3a regulators that is 
wired before the servo power switch the other regulators wired 
after the switch provide 5v for 4 servos each , only pwm and gnd 
signals go from the arduinos to the servos directly
the pots on each leg are wired between the ardunio 5v and gnd 
with the wipres connected to the appropriate analog in
the foot switch is connected between the same 5v and the input
with a 4k7 pulldown resistor to ground 


arduino nano pinouts 
--------------------

              usb connector 
d13  rdy_out         step_rdy_a_in d12
3v3                  hip1_servo    d11/pwm
ref                  leg1_servo    d10/pwm
a0   hip1_pot        knee1_servo   d9 /pwm
a1   leg1_pot        adr1          d8
a2   knee1_pot       adr0          d7
a3   foot_1          hip2_servo    d6 /pwm
a4   hip2_pot        leg2_servo    d5 /pwm
a5   leg2_pot        step_rdy_b_in d4
a6   knee2_pot       knee2_servo   d3 /pwm
a7   foot_2          exception_in  d2
5v                                 gnd
rst                                rst
gnd                  srl tx data   rx0
vin                  srl rx data   tx1
         6 pin isp connector
*/
//
// **********************************************************************
// TODO:-  FIXME:- (high prioraty)
//
// 1/. sort out pwm pll lock , should lock all servos in start positions
// from power up 
//   
//
// TODO:- (low prioraty)  :-
//
// (aditional features)
//  define the serial command functions for :-
//
//    #7                    = not yet defined
//               
//    #8                    = not yet defined
//
//  and sort out the code for them 
//
//  i/o signal pins d2 , d4 , d12  are defined but not used as there
//  orignial intended task is now handled over serial  so are available 
//  for other uses 
// 
//
// **********************************************************************
// 
// serial message format for transmissions to rpi3 from this code
//
//  error message formats and codes
//
//    E[1]                            = com frame sync
//    E[2]                            = buffer overrun 
//    E[3,leg,tag,(h,l or k servo) ]  = servo pwm pll lock loss
//    E[WTF.n]                        = something realy bad happened
//
//  status message formats and codes
//
//    f[leg,d,tag,hip,leg,knee]       = new foot down detected
//    f[leg,u,tag]                    = new foot up detected
//    k[#comm((,data,...if any..))]   = ack command recived 
//    l[leg,r,tag]                    = leg reached hold pos and ready
//
//  cal/test mode output format ( all on one line )
//
//  &1[h=[raw]pwm[d],l=[raw]pwm[d],k=[raw]pwm[d],f[t]]  ;&2[h=[raw]pwm[ 
//       d],l=[raw]pwm[d],k=[raw]pwm[d],f[t]]
//
//
// **********************************************************************
// serial message commands format , from rpi3 to this code
//
//    #0                    = home
//            stops current moves/holds and moves legs to home position
//            responce = > k#0
// 
//    #1[n,t,hhh,lll,kkk]   = set new
//            preloads hip leg knee and tag values for leg n
//            responce = > k#1
//
//    #2                    = next
//            last preload values to current values for all legs
//            responce = > k#2
//
//    #3                    = stop
//            current leg positions current hold positions
//            responce = > k#3
//
//    #4                    = next odd
//            last preload values to current values for odd legs
//            responce = > k#4
//
//    #5                    = next even
//            last preload values to current values for even legs
//            responce = > k#5
//
//    #6[n]                 = next individual
//            last preload values to current values for leg n
//            responce = > k#6
//
//    #7                    = not yet defined
//
//    #8                    = not yet defined
//
//    #9                    = leg status
//            serial sends current legs and position status
//            responce = 
//                k#9,[n,hhh,lll,kkk,f,s],[n,hhh,lll,kkk,f,s]
//                where:-
//                        n   = leg nos 
//                        hhh = hip pos scaled adc value
//                        lll = leg pos scaled adc value
//                        kkk = knee pos scaled adc value
//                        f   = foot status ( u = up or d = down)
//                        s   = lock status ( l= lock or m= moving)
//
// **********************************************************************
//                                 includes
// **********************************************************************
//

#include <Servo.h>

//
// **********************************************************************
//                                 varibles
// **********************************************************************
//

// analog inputs
const int hip1_pot    = A0;
const int leg1_pot    = A1;
const int knee1_pot   = A2;
const int foot1_pot   = A3;
const int hip2_pot    = A4;
const int leg2_pot    = A5;
const int knee2_pot   = A6;
const int foot2_pot   = A7;

// digital i/o pins 
const int exception_in_pin  = 2;  // ** pin defined but currently unused 
const int knee2_servo_pin   = 3;  // pwm
const int step_rdy_b_in_pin = 4;  // ** pin defined but currently unused
const int leg2_servo_pin    = 5;  // pwm
const int hip2_servo_pin    = 6;  // pwm
const int adr0_pin          = 7;  // input with pull up
const int adr1_pin          = 8;  // input with pull up
const int knee1_servo_pin   = 9;  // pwm
const int leg1_servo_pin    = 10; // pwm
const int hip1_servo_pin    = 11; // pwm
const int step_rdy_a_in_pin = 12; // ** pin defined but currently unused
const int rdy_out_pin       = 13; // output

// varibles  pot read values

int hip1_pos  = 0;
int leg1_pos  = 0;
int knee1_pos = 0;
int foot1_pos = 0;
int hip2_pos  = 0;
int leg2_pos  = 0;
int knee2_pos = 0;
int foot2_pos = 0;

// varibles  pot read values scailed

int hip1_pos_s  = 0;
int leg1_pos_s  = 0;
int knee1_pos_s = 0;
int foot1       = 0;
int hip2_pos_s  = 0;
int leg2_pos_s  = 0;
int knee2_pos_s = 0;
int foot2       = 0;

// last foot state varibles

int foot1_old = 0 ; 
int foot2_old = 0 ;

// new serial data varibles  

int hip1_new  = 0;
int leg1_new  = 0;
int knee1_new = 0;
int hip2_new  = 0;
int leg2_new  = 0;
int knee2_new = 0;

// pwm servo names

Servo hip1_servo;    
Servo leg1_servo;    
Servo knee1_servo;    
Servo hip2_servo;     
Servo leg2_servo;     
Servo knee2_servo;  
 
//  pwm varibles

int hip1_pwm  = 0;
int leg1_pwm  = 0;
int knee1_pwm = 0;
int hip2_pwm  = 0;
int leg2_pwm  = 0;
int knee2_pwm = 0;

// pwm output varibles

int hip1_pwmo  = 0;
int leg1_pwmo  = 0;
int knee1_pwmo = 0;
int hip2_pwmo  = 0;
int leg2_pwmo  = 0;
int knee2_pwmo = 0;

// hold position varibles

int hip1_hold  = 0;       
int leg1_hold  = 0;       
int knee1_hold = 0;      
int hip2_hold  = 0;       
int leg2_hold  = 0;       
int knee2_hold = 0;       

// input pin varibles

int exception_in  = false;  // **unused
int step_rdy_b_in = false;  // **unused
int adr0          = false;
int adr1          = false;
int step_rdy_a_in = false;  // **unused

// output pin varibles

int rdy_out  = false;   // rdy led
                               
//serial Strings

String inByte    ;
String buff      ;
String nosstr    ;
String tagstr    ;
String hipstr    ;
String legstr    ;
String kneestr   ;
String leg       ;

String hipstr1=buff   ;
String legstr1=buff   ;
String kneestr1=buff  ;
String hipstr2=buff   ;
String legstr2=buff   ;
String kneestr2=buff  ;

// other varibles

int cal    = false ;
int btag   = 0     ;

// individual servos reached new hold pos 
  
int hip1_rdy   = false ;
int leg1_rdy   = false ;
int knee1_rdy  = false ;
int hip2_rdy   = false ;
int leg2_rdy   = false ;
int knee2_rdy  = false ;

// servos in hold pll lock

int hip1_lock  = false ;
int leg1_lock  = false ;
int knee1_lock = false ;
int hip2_lock  = false ;
int leg2_lock  = false ;
int knee2_lock = false ;

// leg ready all servos reached hold lock 

int rdy1       = false ;
int rdy2       = false ;

// robot leg id varibles

int leg1 = 0 ;
int leg2 = 0 ;

// new sequence tags 

int tag1_new  = 0;
int tag2_new  = 0;

// current hold sequence tag

int tag1_hold = 0;
int tag2_hold = 0;

// error code varible

int error     = 0;

//
// **********************************************************************
//     robot dependant configurtion settings and calibration values 
// **********************************************************************
//     these need to be set depending on your actual robots setup 
// **********************************************************************
//
// servo properties , this defines the working pwm range of all servos
// this should be set to the pwm driven rotational range of movment of 
// the servos  , default 180 degree mg996r servos
   
const int pwm_neg90  =0;    //-90 deg rotation pwm value of servos
const int pwm_pos90  =179;  //-90 deg rotation pwm value of servos

// set so that scaled adc values = servo pwm for the range 
// note :-
// min value should be at least = to backlash value (adc range)
// max value must be 1024 - adc range backlash

const int pot_min    = 90;   // 170 for 180 degree servos
const int pot_max    = 930;  // 850 for 180 degree servos

// change if pwm out values need inverting
 
const int hip_d = 0  ;  // 0=normal / 1=invert  pwm out value
const int leg_d = 0  ;  // 0=normal / 1=invert  pwm out value
const int knee_d = 0 ;  // 0=normal / 1=invert  pwm out value

// change if read adc values need inverting

const int hip_a = 0  ;  // 0=normal / 1=invert  adc in value
const int leg_a = 0  ;  // 0=normal / 1=invert  adc in value
const int knee_a = 0 ;  // 0=normal / 1=invert  adc in value

// default backlash range read is of 20 (+-10) as read from adc values
// needs scaleing to the pwm range thats = to 1/4 approx = +-2.5
// as it needs to be an int use 3 and add one more so that you have a
// wider pwm lock range  makes it +-4 , use 4 as the values is used
// in eather direction no need to have it signed

const int backlash_range  = 6 ;  //default backlash value 

// servo home positions  startup position values
const int hip_home = 91  ;
const int leg_home = 1  ;
const int knee_home = 18  ;

//
// **********************************************************************
//                              setup
// **********************************************************************
// this runs once on startup or reset
void setup() 
{
  // define i/o & servo pwm pins 
  
  pinMode(rdy_out_pin, OUTPUT);          //  d13 rdy led
  pinMode(step_rdy_a_in_pin, INPUT);     //  d12 ** defined but unused
  hip1_servo.attach(hip1_servo_pin);     //  d11 pwm hip1
  leg1_servo.attach(leg1_servo_pin);     //  d10 pwm leg1
  knee1_servo.attach(knee1_servo_pin);   //  d9  pwm knee1
  pinMode(adr1_pin, INPUT_PULLUP);       //  d8  adr 1
  pinMode(adr0_pin, INPUT_PULLUP);       //  d7  adr 2
  hip2_servo.attach(hip2_servo_pin);     //  d6  pwm hip2
  leg2_servo.attach(leg2_servo_pin);     //  d5  pwm leg2
  pinMode(step_rdy_b_in_pin, INPUT);     //  d4  ** defined but unused
  knee2_servo.attach(knee2_servo_pin);   //  d3  pwm knee2
  pinMode(exception_in_pin, INPUT);      //  d2  ** defined but unused
  
  // initialize serial communications at 9600 bps:
  Serial.begin(115200);
  delay(200);
  adr0 = digitalRead(adr0_pin);
  adr1 = digitalRead(adr1_pin); 

  // **** debug force set to adr 00
  //adr0 = 0;
  //adr1 = 0;
  // *****
  if ( adr0 == 0 )
    {
      if ( adr1 == 0)
        {
          // adr=00   legs 1&2
          leg1 = 1;
          leg2 = 2;
          cal = false ;
        }
      else
        {
          // adr=01   legs 3&4
          leg1 = 3;
          leg2 = 4;
          cal = false ;           
        }
    }
  else
    {
      if ( adr1 == 0)
        {
          // adr=10   legs 5&6
          leg1 = 5;
          leg2 = 6;  
          cal = false ;     
        }
      else
        {
          // adr=11   calibrate/test mode 
          cal = true;
        }
    } 

  // set inital new, hold and pwm to servo home positions
  hip1_new  = hip_home  ; 
  leg1_new  = leg_home  ; 
  knee1_new = knee_home ;  
  hip2_new  = hip_home  ; 
  leg2_new  = leg_home  ; 
  knee2_new = knee_home ;  

  hip1_hold  = hip1_new  ;
  leg1_hold  = leg1_new  ;
  knee1_hold = knee1_new ;
  hip2_hold  = hip2_new  ;
  leg2_hold  = leg2_new  ;
  knee2_hold = knee2_new ;
   
  hip1_pwm  = hip1_hold  ;  
  leg1_pwm  = leg1_hold  ;  
  knee1_pwm = knee1_hold ;   
  hip2_pwm  = hip2_hold  ;  
  leg2_pwm  = leg2_hold  ; 
  knee2_pwm = knee2_hold ;
   
  // set position  sync id tags
  tag1_hold = 0;   
  tag2_hold = 0;   
  tag1_new  = 0;   
  tag2_new  = 0;   
  
  // set and invert if needed pwmo values 
  if (hip_d == 0)
    {
      hip1_pwmo  =  hip1_pwm  ;
      hip2_pwmo  =  hip2_pwm  ;
    }  
  else 
    {
      hip1_pwmo  = 179 - hip1_pwm  ;
      hip2_pwmo  = 179 - hip2_pwm  ;
    }
  if (leg_d == 0) 
    {
      leg1_pwmo  =  leg1_pwm  ;
      leg2_pwmo  =  leg2_pwm  ;
    }
    else
    {
      leg1_pwmo  = 179 - leg1_pwm  ;
      leg2_pwmo  = 179 - leg2_pwm  ;
    }       
  if (knee_d == 0) 
    {
      knee1_pwmo = knee1_pwm ;       
      knee2_pwmo = knee2_pwm ;      
    }
    else
    {
      knee1_pwmo = 179 - knee1_pwm ;       
      knee2_pwmo = 179 - knee2_pwm ;
    }
  // update pwm i/o values   servo.write(pwmvalout); for all servos
  hip1_servo.write(hip1_pwmo);    
  leg1_servo.write(leg1_pwmo);    
  knee1_servo.write(knee1_pwmo);    
  hip2_servo.write(hip2_pwmo);     
  leg2_servo.write(leg2_pwmo);     
  knee2_servo.write(knee2_pwmo); 

  foot1_old = foot1;
  foot2_old = foot2;
}

//
// **********************************************************************
//                               main code loop
// **********************************************************************
// main code , loops forever
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

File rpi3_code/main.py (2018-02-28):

#!/usr/bin/env python
#
# ****************************************************************************
# * main.py      main robot control program for leggie hexapod               *
# ****************************************************************************
# * version  1.0a                                              15th feb 2018 *
# ****************************************************************************
# *      (c)2018 & written by  David Powell  (A.K.A AchiestDragon)           *
# ****************************************************************************
#  license  GPL v3 
#
#     !!!!!!!!!!!!!!! THIS IS ALPHA CODE AND NOT COMPLETE !!!!!!!!!!!!!!!!
#
# description :-
#
#  WORK IN PROGRESS NOT YET FUNCTIONAL 
#
# TODO:-   almost everything
#
#   1. add support for remote joystick serial connection over 
#        a:-  serial over ip (wifi/ethernet) 
#        b:-  bluetooth
#        c:-  where the joystick has bluetooth dongle fitted
#
#   2. debug code (not all for inclusion in final version but for testing during
#      writing the code) mainly direct servo positon  in relation to joystick
#      position , this code is to be made selectable on the command line >>>
#
#      add the following command line options 
#      >>> j       joystick moves servos directly  (debug code only)
#      >>> v       toggle verbose joystick position data
#      >>> s       toggle verbose serial tx data stream 
#      >>> r       toggle verbose recive serial data
#      >>> d       full leg status for all legs 
#      >>> h       home all legs
#
#   3. add code for calculating direction movements to new footing
#      positions and calculate the walking gate sequence from 
#      direction inputs to feed into the walking sequence buffers
#
#   4. fixed sequence movements and other sequencing code    
#
#   5. ...all the other things 
#
#   6. a gui control interface ? (maybe someday)
#
# FIXME:- 
#
#   1. serial write command thread dropping out of sequence
#      fix rewrite  srl_write_queue_worker( srl_out_q, ): as a callable
#      function  ser_out(ser_out_d): with single string input not a queue 
#

#
# ****************************************************************************
# *                               imports                                    *
# ****************************************************************************
#

import sys
import tty
import termios
import threading
import time
import serial
import Queue

#
# ****************************************************************************
# *                         serial read worker                               *
# ****************************************************************************
#

def srl_worker(num , srl_in_q , ):
    if num == 0:
        print 'Started Serial Read Worker:1 on port : /dev/ttyUSB0'
        counter0=0
        if ser0.isOpen():
            while exit != 1 :
                x0=ser0.readline()
                x0=x0.strip('\r\n')
                if x0 != '':               
                    if x0.startswith('E[1')==True : 
                        print "CRITICAL serial com sync error, from :- /dev/ttyUSB0 with :-",x0 
                        print "program EXIT forced "
                        Exit(1)
                    if x0.startswith('E[2')==True :
                        print "CRITICAL serial com buffer overrun , from :-/dev/ttyUSB0 with :-",x0
                        print "program EXIT forced "
                        Exit(1)
                    if x0.startswith('E[W')==True :
                        print "CRITICAL WTF error , from :-/dev/ttyUSB0 with:-" , x0
                        print "program EXIT forced "
                        Exit(1)
                    if x0.startswith('E[3,')==True :
                        print "ERROR pwm pll lock loss , from :- /dev/ttyUSB0 with :-" , x0
                        srl_in_q.put(x0)
                    if x0.startswith('k')== True :
                        srl_in_q.put(x0)
                    if x0.startswith('f[')== True :
                        srl_in_q.put(x0)
                    if x0.startswith('l[')== True :
                        srl_in_q.put(x0)
                    if x0.startswith('&')== True :
                        print "CRITICAL device in calibration mode from :-/dev/ttyUSB0 "
                        print "with:-" , x0
                        print "program EXIT forced "
                        Exit(1)
                    if x0.startswith('[')== True :  
                        srl_in_q.put(x0)
                    
            print 'Serial Read Worker:1 exit'
        else:
            slr_in_q.put('E[ser0]')
        return 
    if num == 1:
        print 'Started Serial Read Worker:2 on port : /dev/ttyUSB1'
        counter1=0
        if ser1.isOpen():
            while exit != 1 :
                x1=ser1.readline()
                x1=x1.strip('\r\n')
                if x1 != '':               
                    if x1.startswith('E[1')==True :
                        print "CRITICAL serial com sync error, from :- /dev/ttyUSB1 with:-",x1
                        print "program EXIT forced "
                        Exit(1)
                    if x1.startswith('E[2')==True :
                        print "CRITICAL serial com buffer overrun , from :-/dev/ttyUSB1 with:-",x1
                        print "program EXIT forced "
                        Exit(1)
                    if x1.startswith('E[W')==True :
                        print "CRITICAL WTF error , from :-/dev/ttyUSB1 with:-" , x1
                        print "program EXIT forced "
                        Exit(1)
                    if x1.startswith('E[3,')==True :
                        print "ERROR pwm pll lock loss , from :- /dev/ttyUSB1 with :-" , x1
                        srl_in_q.put(x1)
                    if x1.startswith('k')== True :
                        srl_in_q.put(x1)
                    if x1.startswith('f[')== True :
                        srl_in_q.put(x1)
                    if x1.startswith('l[')== True :
                        srl_in_q.put(x1)
                    if x1.startswith('&')== True :
                        print "CRITICAL device in calibration mode from :-/dev/ttyUSB1 "
                        print "with:-" , x1
                        print "program EXIT forced "
                        Exit(1)
                    if x1.startswith('[')== True : 
                        srl_in_q.put(x1)
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

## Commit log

2018-02-07 my snapshot
    [base_bottom.stl, base_sup.stl, base_upper.stl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]
2018-02-08 almost ready , command decode fixed
    [leggie_arduino_pid.ino]
2018-02-09 bugfix , initial testing
    [leggie_arduino_pid.ino]
2018-02-09 more fixes ..... :)
    [leggie_arduino_pid.ino]
2018-02-10 todo / fixme status update
    [leggie_arduino_pid.ino]
2018-02-11 fixes and debug (still problems)
    [leggie_arduino_pid.ino]
2018-02-11 adc to pwm position scale range fix
    [leggie_arduino_pid.ino]
2018-02-11 set pwm out values fixed (test only)
    [leggie_arduino_pid.ino]
2018-02-11 debug pwm test code
2018-02-12 removed fixed pwm output values
    [leggie_arduino_pid.ino]
2018-02-13 serial command decode fixed , debug removed
    [leggie_arduino_pid.ino]
2018-02-13 some fixes and commmand #9 added
    [leggie_arduino_pid.ino]
2018-02-13 comments fixed , version bump to 1.0b
    [USBjoystick1.ino]
2018-02-14 fixed thread id start messages
    [srlpy.py]
2018-02-16 work in progress ,( broken )
    [main.py]
2018-02-16 (still broken) added FIXME:- comments
    [main.py]
2018-02-17 lower leg v2 (lenth changed)
    [leggie4.scad, lower_leg_v2.stl]
2018-02-17 file in wrong dir
    [lower_leg_v2.stl]
2018-02-17 updated (v2 lower leg):
    [leggie4.scad]
2018-02-18 ok so missed a few ":"'s
    [main.py]
2018-02-18 fixes ? may work
    [main.py]
2018-02-18 ok so maybe not ... fix
    [main.py]
2018-02-18 fixing srl error and config
    [main.py]
2018-02-18 serial command routing fixed ?
    [main.py]
2018-02-18 more added . may need fixing
    [main.py]
2018-02-18 exit code gracefully fix ?
    [main.py]
2018-02-19 var name srl_out_q not ser_out_que fixed
    [main.py]
2018-02-19 time func fix format
    [main.py]
2018-02-19 close threads and gracefully exit, a fix fix
    [main.py]
2018-02-19 fix for ,exit correctly
    [main.py]
2018-02-19 serial input decode part1 added (error decode)
    [main.py]
2018-02-19 command case k not K
2018-02-19 updated pwm pll foot lock overide
2018-02-19 init serial fix 1
    [main.py]
2018-02-19 fix 4fix 4fix 4fix 4
    [main.py]
2018-02-20 fixed missing var def
    [main.py]
2018-02-20 startup progress bar fix
    [main.py]
2018-02-20 console message format fix
    [main.py]
2018-02-20 fix serial with joystick
    [main.py]
2018-02-20 joystick decode fix xyz
    [main.py]
2018-02-20 joystick button decodes added
2018-02-20 servo joystick test
2018-02-20 servo test set current to new
2018-02-20 print debug outstr
2018-02-21 console prints :-line formating
2018-02-21 stop scrolling on joystick data print fix
    [main.py]
2018-02-21 servo debug via direct joystick control
2018-02-22 test coe serial ack fix
    [main.py]
2018-02-22 serial k[ack] message fix for #1
    [leggie_arduino_pid.ino, main.py]
2018-02-22 serial #1 command decode fix
    [leggie_arduino_pid.ino]
2018-02-23 updated todo/fixme for needed changes
    [main.py]
2018-02-23 direct serial control only (-pid -pwm)
2018-02-23 joystick to position servo drive change
2018-02-23 joystick scail values to pwm direct
2018-02-23 fix == and : syntax
    [main.py]
2018-02-27 button1 sequence added
2018-02-27 button1 fix
2018-02-27 button1 fix ==
2018-02-28 thread to function call fix
    [main.py]
2018-02-28 missing ' ' indent fix
    [main.py]
2018-02-28 function name clash fix
    [main.py]
2018-02-28 global var def fix
    [main.py]
2018-02-28 debug print srl_out_d on send
2018-03-02 directory name change
    [base_bottom.stl, base_sup.stl, base_upper.stl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]
2018-03-02 shape lib and first 2 parts added
    [actuator_shaft_rail.scad, actuator_shaft_rail.stl, carrage_half.scad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]
2018-03-02 assembly notes and fig/.1 added
2018-03-02 assembly instruction updates:
2018-03-03 upper leg cad files added
    [leg_half.scad, leg_half.stl, parts_lib.scad]
2018-03-03 leg half part update
    [leg_half.scad, leg_half.stl]
2018-03-04 leg joint parts added
    [leg_joint.scad, leg_joint.stl]
2018-03-04 right way up for printing
    [leg_joint.stl]
2018-03-04 part updated
    [leg_joint.scad, leg_joint.stl]
2018-03-06 part added
    [conrod.scad, conrod.stl]
2018-03-08 derived from thingverse #10848 5mm hole
    [t5a.stl]
2018-03-09 part updates
    [leg_half.scad]
2018-03-11 more parts added
    [hip_pivot.scad, hip_pivot.stl, hip_slide.scad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]
2018-03-13 more bits added # Please enter the commit message for your changes. Lines starting
    [base_asembled.scad, leg_joints.scad]
2018-03-14 part additions and updates
    [base_asembled.scad, base_bottom.stl, base_center.stl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]
2018-03-16 addidtions and updates
    [base_asembled.scad, leg_joint.scad, leg_joint.stl]
2018-03-16 updates and additions
    [leg_joint.scad, leg_joints.scad, lower_leg.stl]
2018-04-02 parts added
    [foot.scad, foot_mnt.stl, footpad.stl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]
2018-04-13 added conrod_spacer
    [conrod_spacer.scad, conrod_spacer.stl]
2018-04-18 motor driver pcb mounting frame added
    [base_asembled.scad]
2018-04-23 parts added and updated
    [base_asembled.scad, bodymount.stl, spacerframe.stl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]
2018-04-27 remove old servo version stl / scad files
    [base_bottom.stl, base_sup.stl, base_upper.stl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]
2018-04-27 added joystick rc controler box scad/stl files
    [rc.scad, rcbox.stl, rcboxlid.stl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]
2018-05-09 schematic files added
    [kicad_h-bridge.sch]
2018-05-09 more schematics added (still some to do)
    [if_control.sch, rpi_if_cable.sch]
2018-05-09 schematics updated
    [if_control.sch, rpi_if_cable.sch]
2018-05-10 tidy dir
    [if_control.sch, kicad_h-bridge.sch, power_dist.sch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]
2018-05-10 pic updated (current progress)
